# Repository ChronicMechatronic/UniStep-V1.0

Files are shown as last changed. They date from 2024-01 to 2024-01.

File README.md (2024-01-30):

# UniStep-V1.0
UniStep v1 0 -removebg-preview

UniStep is a simple, low-cost, translating stepper motor driver allowing you to use cheaply manufactured unipolar steppers frequently found in e-waste for any kind of CNC project like 3D printers, 
without doing the usual unipolar-to-bipolar mod needed in order to use common bipolar drivers like the A4988. 
Driving them in their original unipolar configuration makes the motors a lot quieter as current limiting relies on the internal phase resistance of the motor rather than a noisy PWM signal in constant current control.
Of course unipolar motors also have a number of disadvantages over their bipolar hybrid counterparts, (notably: lower max speeds, faster torque drop-off at high speeds, commonly low resolution of only 48 steps/revolution) making them 
indesirable for 3D printing and laser cutting (basically all direct belt drive applications). For many low-stake automation tasks they're usually sufficient though and being able to reuse e-waste is worth something as well, so this translating driver makes it easier.

Taking step/direction and enable input signals UniStep is fully compatible with the well established A4988 ecosystem, allowing to easily retrofit existing hardware.

Specifications:

-A4988 hardware compatible

-Max. voltage: 28V

-Max. current per phase: 0.5A (plenty for all unipolar motors I've so far come across)

-Microstepping mode: halfsteps (can be changed to fullsteps in software, though I'm not sure know why you'd ever do that)

Pinout diagram:

pinout small

For more detailed explanations and assembly instructions watch my full video on YouTube:

(https://youtu.be/VZYx2AsjqHE)

Notes:
Since current is purely limited by the motor's phase resistance, the supply voltage must be matched to the motor. Otherwise overheating may occur.

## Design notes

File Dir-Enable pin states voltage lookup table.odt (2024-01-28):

Known Pin States (high or low) | ENABLE floating (breadboard) | Plugged into RAMPS 1.4 (ENABLE high + 10kΩ)

ENABLE | DIRECTION | VOLTAGE | ENABLE | DIRECTION | VOLTAGE | ENABLE | DIRECTION | VOLTAGE
LOW | LOW | 0.0V | N/A | LOW | 0.0V | LOW | LOW | 0.0V
LOW | HIGH | 2.5V | N/A | HIGH | 2.5V | LOW | HIGH | 2.5V
HIGH | LOW | ~ 5.0V | N/A | LOW | 0.0V | HIGH | LOW | 3.57V
HIGH | HIGH | ~ 5.0V | N/A | HIGH | 2.5V | HIGH | HIGH | 4.254V

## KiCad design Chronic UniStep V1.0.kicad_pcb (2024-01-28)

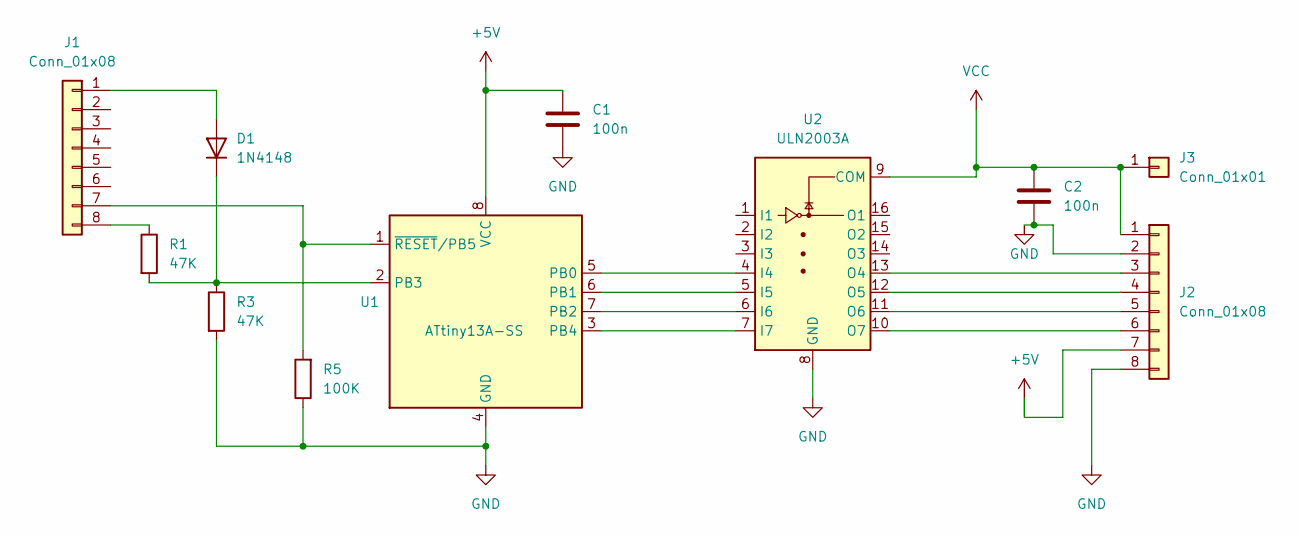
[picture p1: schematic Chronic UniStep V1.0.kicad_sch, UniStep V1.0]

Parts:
C1, C2: 100n; C_0603_1608Metric
D1: 1N4148; D_SOD-323
J1, J2: Conn_01x08; PinHeader_1x08_P2.54mm_Vertical
J3: Conn_01x01; PinHeader_1x01_P2.54mm_Vertical
R1, R3: 47K; R_0603_1608Metric
R5: 100K; R_0603_1608Metric
U1: ATtiny13A-SS; SOIC-8W_5.3x5.3mm_P1.27mm
U2: ULN2003A; SOIC-16_3.9x9.9mm_P1.27mm

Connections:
+5V: C1.1, J2.7, U1.8 (VCC)
GND: C1.2, C2.2, J2.2, J2.8, R3.2, R5.1, U1.4 (GND), U2.8 (GND)
unnamed: D1.1 (K), R1.2, R3.1, U1.2 (PB3)
unnamed: D1.2 (A), J1.1
unnamed: J1.7, R5.2, U1.1 (~RESET/PB5)
unnamed: J1.8, R1.1
unnamed: J2.4, U2.12 (O5)
unnamed: U1.5 (PB0), U2.4 (I4)
unnamed: U1.6 (PB1), U2.5 (I5)
unnamed: U1.7 (PB2), U2.6 (I6)
unnamed: U1.3 (PB4), U2.7 (I7)
unnamed: J2.6, U2.10 (O7)
unnamed: J2.5, U2.11 (O6)
unnamed: J2.3, U2.13 (O4)
VCC: C2.1, J2.1, J3.1, U2.9 (COM)

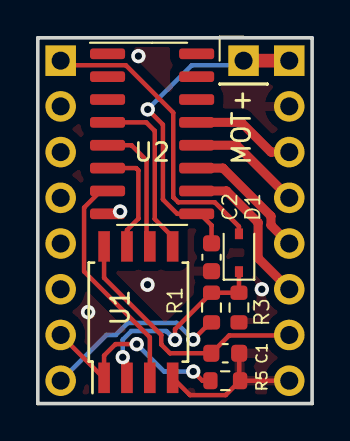
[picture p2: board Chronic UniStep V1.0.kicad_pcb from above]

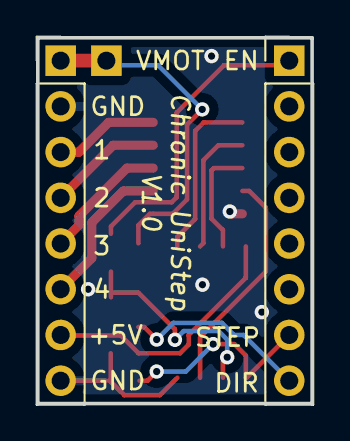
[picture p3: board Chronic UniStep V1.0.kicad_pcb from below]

Board: 2 copper layers, 15.2 x 20.3 mm, 11 parts (2 on the bottom side), 15 nets.

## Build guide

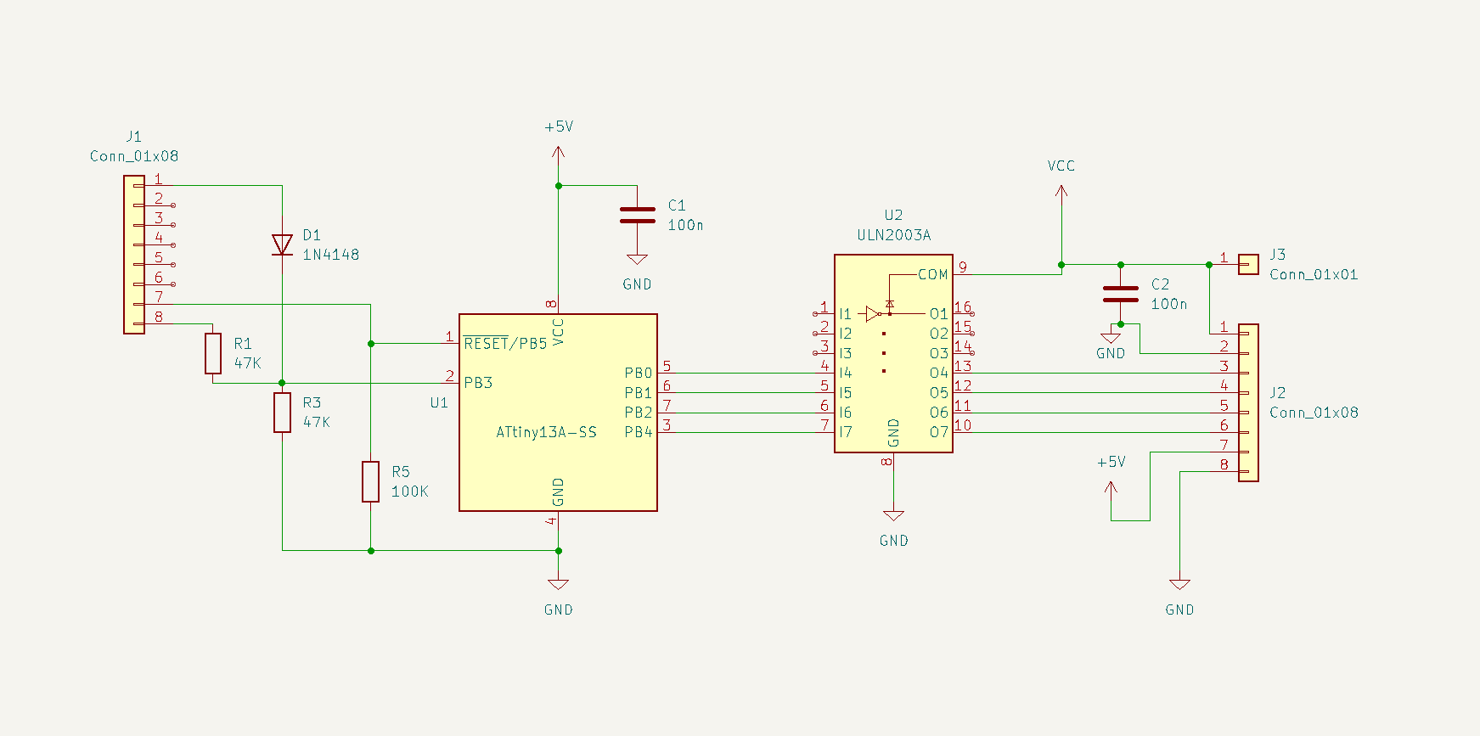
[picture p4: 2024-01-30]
UniStep V1.0 schematic.png

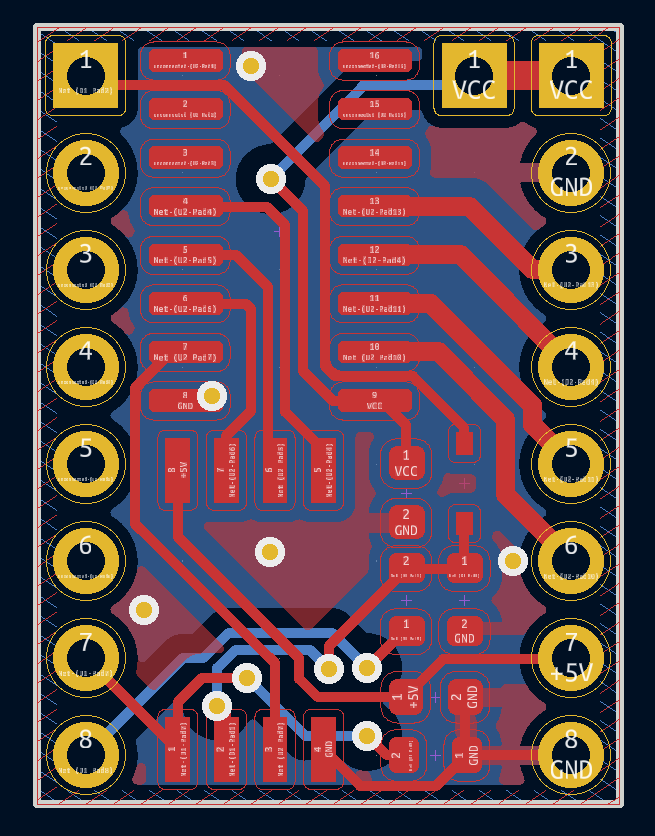
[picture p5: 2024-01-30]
UniStep V1.0 PCB layout.png

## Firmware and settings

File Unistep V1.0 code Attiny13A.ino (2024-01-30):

/*100% functional UniStep code for Attiny13A
Distributed under the GPL-3.0 V3 license
01/28/2024 by Chronic Mechatronic
With modifications suggested by Flo (change variables to uint8/16_t; add default case to switch statement)
and tested. (Attiny can be erased and reprogrammed in-situ)

Requires following voltage divider on PB3:
47K resistor from sensepin to ground, 47K resistor from sensepin to DIR input, generic diode from ENABLE input to sensepin (cathode connects to sensepin)
*/

#include <avr/io.h>
#include <avr/interrupt.h>

//input pins:
#define StepIn PB5
#define DirEnableIn PB3

volatile bool direction = 0;   //boolean for CW or CCW rotation
volatile uint8_t StepCount = 1;   // step counter variable
uint16_t DirEnval = 0;



void setup() {

  DDRB = DDRB | B00010111; //set PB3 and PB5 as inputs, the rest as outputs using direct port manipulation

  // Enable the pin change interrupt for PB0
  PCMSK |= _BV(PCINT5);
  GIMSK |= _BV(PCIE);
  
}





void loop() {
  
  DirEnval = analogRead(DirEnableIn);   //read analog input voltage for the combined direction/enable pin

  //set direction variable true or false depending on the voltage measured on the resistor divider. True = clockwise and false = anticlockwise
  if(DirEnval<256) {direction=false;}                         //direction of rotation is CCW if measured voltage under 1.25V
  else if(DirEnval>256 && DirEnval<600) {direction=true;}     //direction of rotation is CW if voltage between 1.25V and 2.93V

  while(analogRead(DirEnableIn)>600) {           //turn motor off while enable input is high
    PORTB = B00000000;
  }

    

  switch(StepCount) {               //Main step execution. Switches PB0 through PB4 via direct port manipulation depending on the current position in the halfstep sequence
    case 1:
    PORTB = B00000001;
    break;
    
    case 2:
    PORTB = B00000011;
    break;
    
    case 3:
    PORTB = B00000010;
    break;
    
    case 4:
    PORTB = B00000110;
    break;
    
    case 5:
    PORTB = B00000100;
    break;
    
    case 6:
    PORTB = B00010100;
    break;
    
    case 7:
    PORTB = B00010000;
    break;
    
    case 8:
    PORTB = B00010001;
    break;    
  
    default:
    PORTB = B00000000;    // turn off motor in case StepCount variable doesn't match expected value
    break;
  }



} //end of void loop



ISR (PCINT0_vect) {       //interrupt service routine: counts the step sequence up or down depending on the last known state of the direction pin

if(!digitalRead(StepIn)){ /*do nothing for interrupts triggered by a falling edge*/ }
else{

  if(direction){StepCount++;}       //advance step sequence if direction CW, lower count if CCW
  else {StepCount--;}
 

  if(StepCount>8) {StepCount=1;}          //reset step counter to keep count within the 8 designated halfsteps
  else if(StepCount<1) {StepCount=8;}   
}

}

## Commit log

2024-01-28 Add schematic and board files
    [Chronic UniStep V1.0.kicad_pcb, Chronic UniStep V1.0.kicad_sch]
2024-01-28 Add gerber files
2024-01-28 Add voltage LUT
2024-01-28 Update Unistep V1.0 code Attiny13A.ino
    correct date typo
    [Unistep V1.0 code Attiny13A.ino]
2024-01-30 Add schematic and PCB layout pics
